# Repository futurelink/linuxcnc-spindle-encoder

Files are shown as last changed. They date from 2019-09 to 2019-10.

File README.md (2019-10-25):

# Incremental encoder Modbus RTU interface

This device is an interface to read incremental encoder meanings with Modbus.
It supports encoders from 100 to 1000PPR and interpolate position up to 4 times, 
so maximum resolutuion is 4000PPR. 

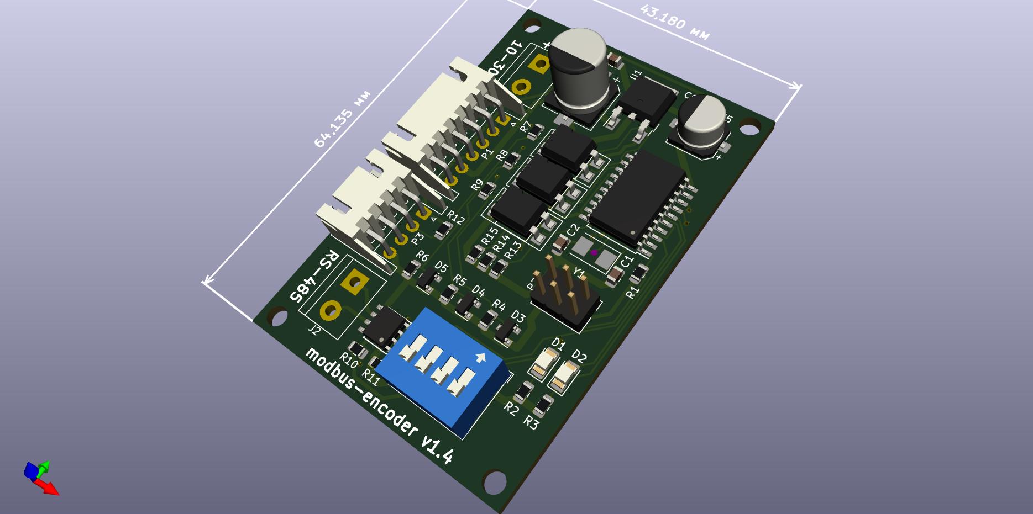
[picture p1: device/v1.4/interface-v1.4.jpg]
Device KiCAD 3D view


It's tested on 1000PPR encoder and it reads correct values on about 1000RPMs on internal 8MHz
ATtiny2313 RC oscillator, and about 2000PPM on 16MHz crystal.

## What does it do?

This small attiny2313 module and LinuxCNC component allows you to connect almost any precision encoder into LinuxCNC
and it works even if it has no Z phase output.

It allows your lathe execute G33, G33.1 (synchronized motion) and G76 (threading) canned cycles and 
use G96 (constant surface speed) spindle control strategy.

## Modbus

Device has slave ID 0x85. There are 6 16bit analog registers starting from reference address 0x00,
containing (0)heartbeat, (1)current position, (2)position increment, (3)current speed in RPM, (4)current Z-index value
and (5)encoder direction.

Device UART speed is 38400bps.

## Connection to LinuxCNC

Go to ./linuxcnc and execute:

```
$ sudo make
```

This will install component into your LinuxCNC.

Then you need this component in your HAL:

```
loadrt spindle_encoder
addf spindle-encoder.0 servo-thread
setp spindle-encoder.0.ppr 4096
net spindle-heartbeat  spindle-encoder.0.heartbeat <= mb2hal.spindle-encoder.heartbeat.int
net spindle-pos-in     spindle-encoder.0.pos-in <= mb2hal.spindle-encoder.pos-in.float
net spindle-pos-out    spindle-encoder.0.pos-out => motion.spindle-revs
net spindle-speed-rpm  spindle-encoder.0.speed-rpm <= mb2hal.spindle-encoder.speed-rpm.int
net spindle-speed      spindle-encoder.0.speed-rps => motion.spindle-speed-in
net spindle-index      spindle-encoder.0.index-in <= mb2hal.spindle-encoder.index.int
net spindle-index-ena  spindle-encoder.0.index-enable <=> motion.spindle-index-enable
net spindle-dir        spindle-encoder.0.direction <= mb2hal.spindle-encoder.direction.int
```

Also you'll need to load mb2hal module into userspace:

```
loadusr -W mb2hal config=modbus_config.ini
```

Copy modbus_config.ini from ./linuxcnc into your lathe configuration directory. Write your serial 
port device to SERIAL_PORT option in that ini file. Correct SERIAL_DELAY_MS if you need.

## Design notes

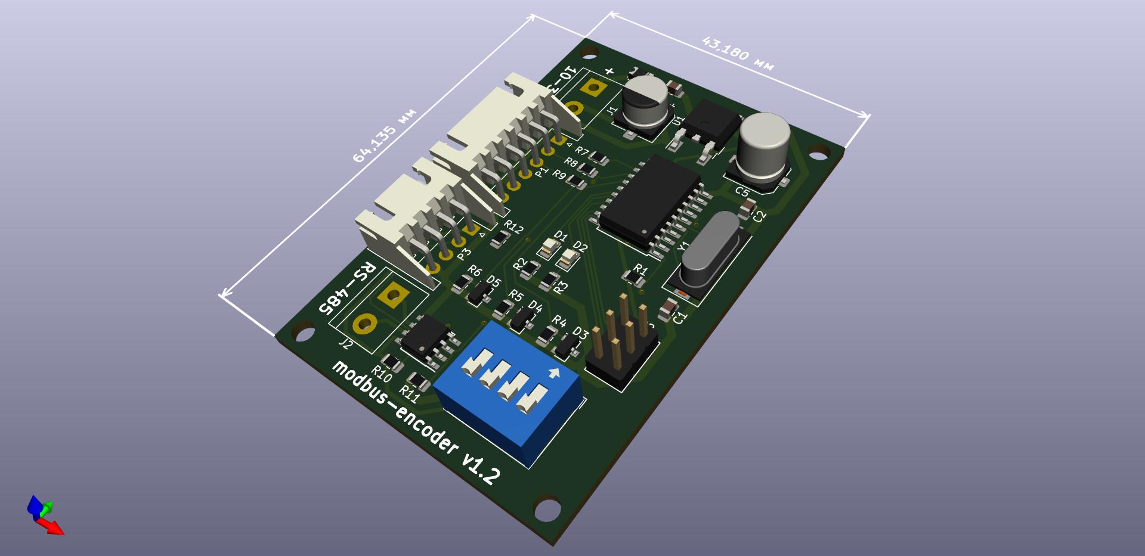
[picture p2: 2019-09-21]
device/interface-v1.2.jpg

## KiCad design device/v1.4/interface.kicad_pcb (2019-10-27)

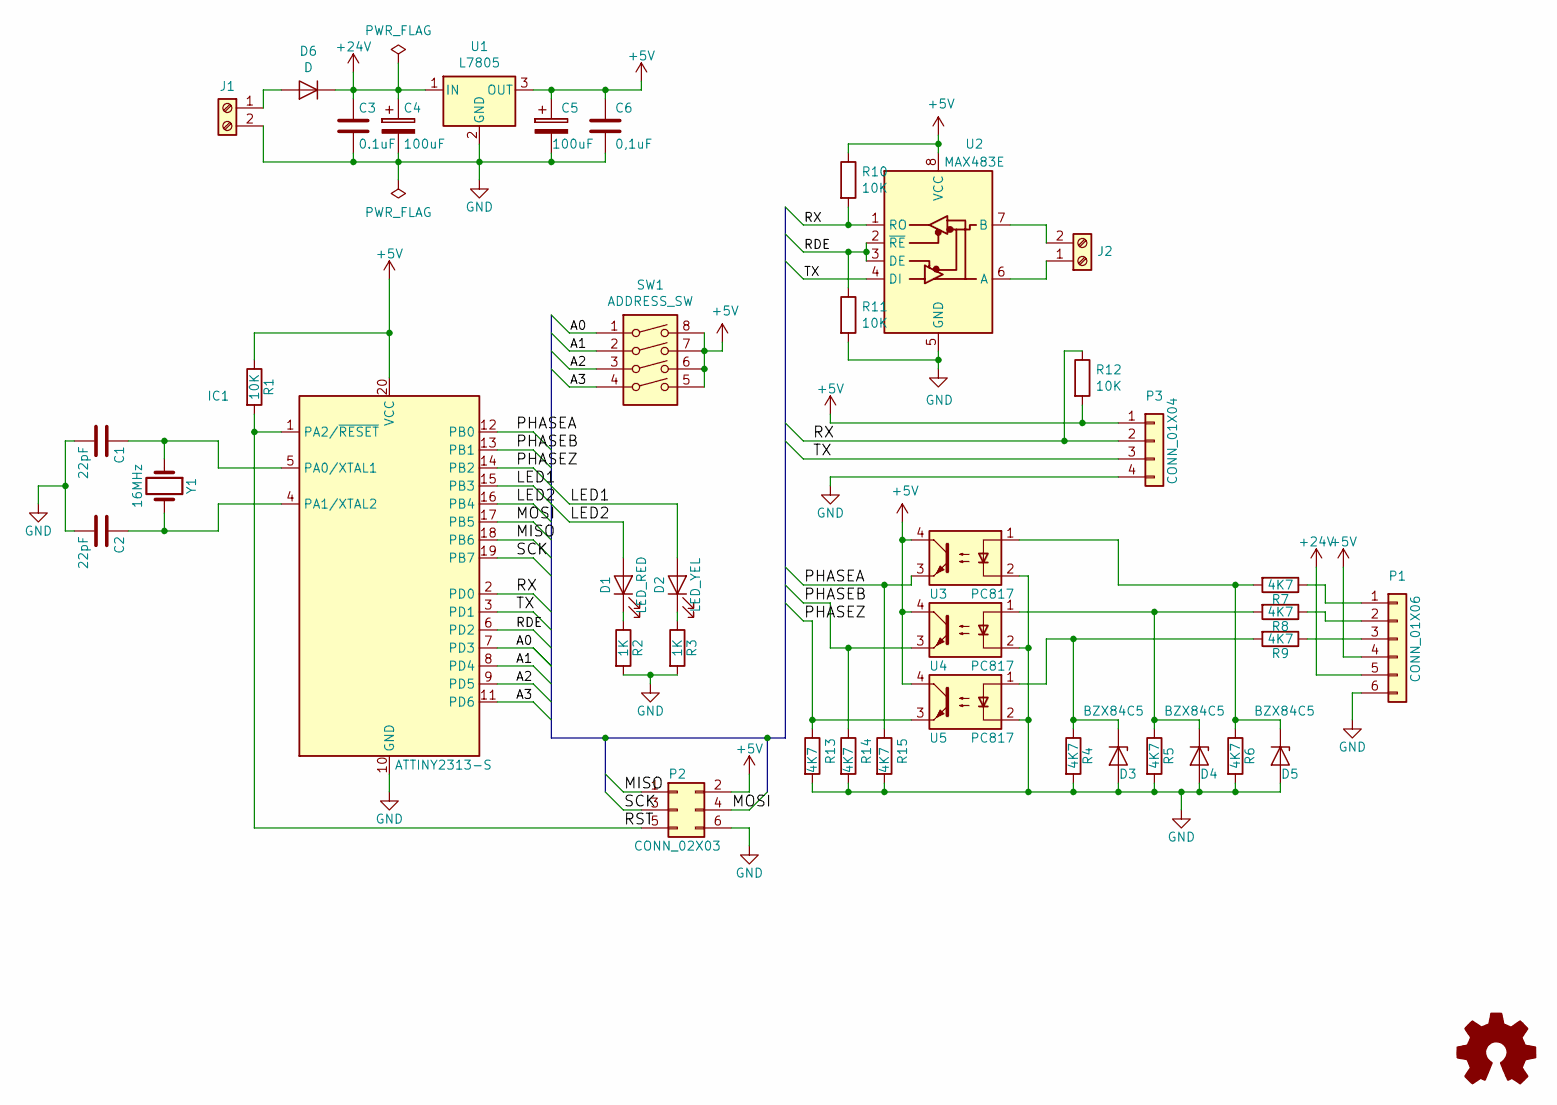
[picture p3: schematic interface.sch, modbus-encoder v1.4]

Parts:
C1, C2: 22pF; C_0805_2012Metric
C3: 0.1uF; C_0805_2012Metric
C4: 100uF; CP_Elec_8x10.5
C5: 100uF; CP_Elec_6.3x5.3
C6: 0,1uF; C_0805_2012Metric
D1: LED_RED; LED_1206_3216Metric
D2: LED_YEL; LED_1206_3216Metric
D3, D4, D5: BZX84C5; D_SOT-23_ANK
D6: D; D_1206_3216Metric
IC1: ATTINY2313-S; SOIC-20W_7.5x12.8mm_P1.27mm
J1: Screw_Terminal_1x02; TerminalBlock_bornier-2_P5.08mm
J2: Screw_Terminal_01x02; TerminalBlock_bornier-2_P5.08mm
P1: CONN_01X06; JST_XH_S6B-XH-A_1x06_P2.50mm_Horizontal
P2: CONN_02X03; PinHeader_2x03_P2.54mm_Vertical
P3: CONN_01X04; JST_XH_S4B-XH-A_1x04_P2.50mm_Horizontal
R1, R10, R11, R12: 10K; R_0805_2012Metric
R2, R3: 1K; R_0805_2012Metric
R4, R5, R6, R7, R8, R9, R13, R14, R15: 4K7; R_0805_2012Metric
SW1: ADDRESS_SW; SW_DIP_SPSTx04_Slide_9.78x12.34mm_W7.62mm_P2.54mm
U1: L7805; TO-252-2
U2: MAX483E; SOIC-8_3.9x4.9mm_P1.27mm
U3, U4, U5: PC817; DIP-4_W7.62mm_SMDSocket_SmallPads
Y1: 16MHz; Crystal_SMD_5032-2Pin_5.0x3.2mm

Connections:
+5V: C5.1, C6.1, IC1.20 (VCC), P1.4, P2.2, P3.1, R1.1, R10.1, R12.2, SW1.5, SW1.6, SW1.7, SW1.8, U1.3 (OUT), U2.8 (VCC), U3.4, U4.4, U5.4
+24V: C3.1, C4.1, D6.1 (K), P1.5, U1.1 (IN)
/A0: IC1.7 (PD3), SW1.1
/A1: IC1.8 (PD4), SW1.2
/A2: IC1.9 (PD5), SW1.3
/A3: IC1.11 (PD6), SW1.4
/LED1: D2.2 (A), IC1.15 (PB3)
/LED2: D1.2 (A), IC1.16 (PB4)
/MISO: IC1.18 (PB6), P2.1
/MOSI: IC1.17 (PB5), P2.4
/PHASEA: IC1.12 (PB0), R15.1, U3.3
/PHASEB: IC1.13 (PB1), R14.1, U4.3
/PHASEZ: IC1.14 (PB2), R13.1, U5.3
/RDE: IC1.6 (PD2), R11.1, U2.2 (~RE), U2.3 (DE)
/RST: IC1.1 (PA2/~RESET), P2.5, R1.2
/RX: IC1.2 (PD0), P3.2, R10.2, R12.1, U2.1 (RO)
/SCK: IC1.19 (PB7), P2.3
/TX: IC1.3 (PD1), P3.3, U2.4 (DI)
GND: C1.2, C2.2, C3.2, C4.2, C5.2, C6.2, D3.2 (A), D4.2 (A), D5.2 (A), IC1.10 (GND), J1.2, P1.6, P2.6, P3.4, R2.2, R3.2, R4.2, R5.2, R6.2, R11.2, R13.2, R14.2, R15.2, U1.2 (GND), U2.5 (GND), U3.2, U4.2, U5.2
unnamed: C1.1, IC1.5 (PA0/XTAL1), Y1.1
unnamed: C2.1, IC1.4 (PA1/XTAL2), Y1.2
unnamed: D1.1 (K), R2.1
unnamed: D2.1 (K), R3.1
unnamed: D3.1 (K), R4.1, R9.2, U5.1
unnamed: D4.1 (K), R5.1, R8.2, U4.1
unnamed: D5.1 (K), R6.1, R7.2, U3.1
unnamed: D6.2 (A), J1.1
unnamed: J2.1, U2.6 (A)
unnamed: J2.2, U2.7 (B)
unnamed: P1.1, R7.1
unnamed: P1.2, R8.1
unnamed: P1.3, R9.1

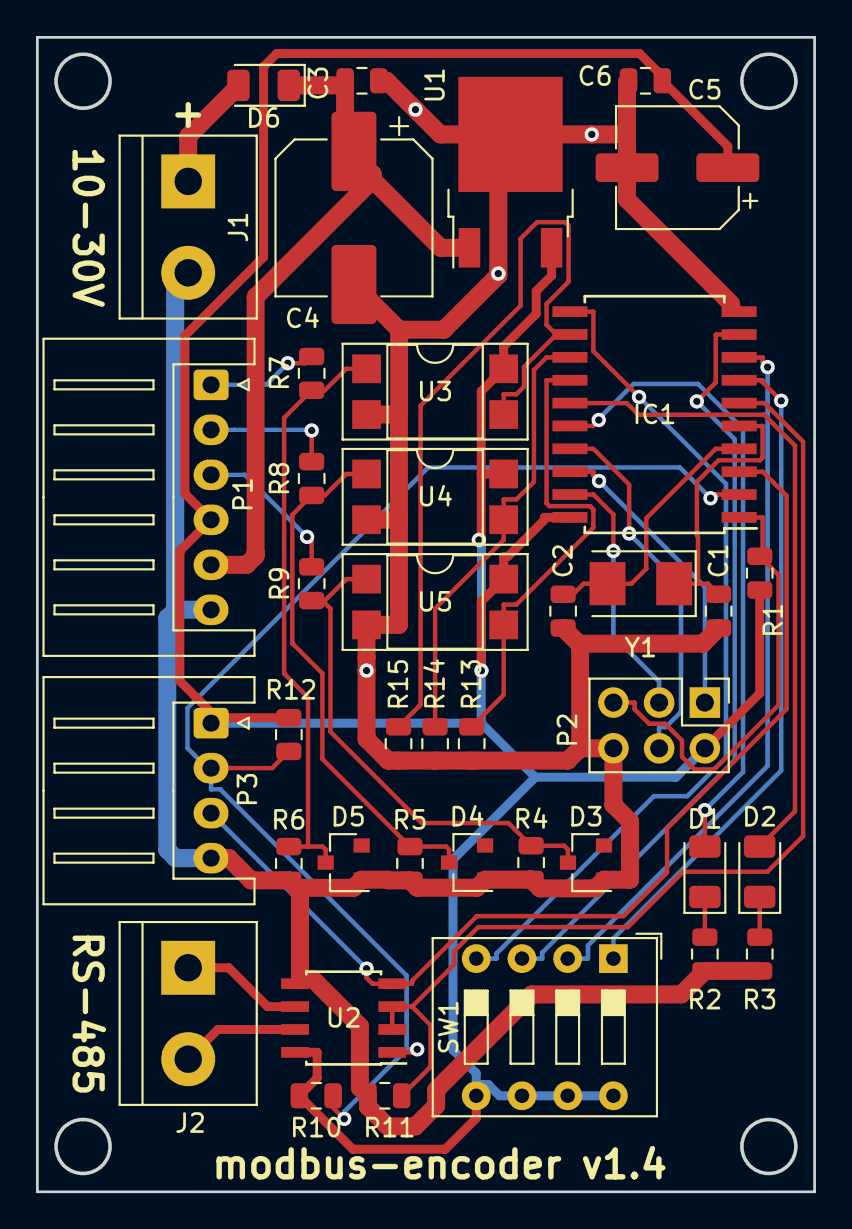
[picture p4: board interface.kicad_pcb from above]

Board: 2 copper layers, 43.2 x 64.1 mm, 40 parts (0 on the bottom side), 32 nets.

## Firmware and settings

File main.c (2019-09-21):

/*

Copyright 2019 Pavlov Denis <futurelink.vl@gmail.com>

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
*/

#include <avr/wdt.h>
#include <avr/io.h>
#include <avr/interrupt.h>

#include "config.h"

#define PARITY_NONE	0
#define PARITY_ODD	1
#define PARITY_EVEN	2

static void initPorts(void);
static void initUSART(uint8_t parity);
static void initTimer1(uint8_t timeout50usTicks);
static void initTimer0(void);

extern uint8_t slaveAddr;
extern volatile uint8_t sentLength;
extern volatile uint8_t sendLength;
extern uint8_t sendBuffer[];

int main(void) {
    asm("WDR");
    MCUSR &= ~(1 << WDRF);
    WDTCSR |= (1 << WDCE) | (1 << WDE);
    WDTCSR = (1 << WDE) | (1 << WDP2) | (1 << WDP1); // Вотчдог через 1 сек

    initUSART(PARITY_NONE);
    initTimer1(35);
    initTimer0();
    initPorts();

    sei();

    PORTB |= (1 << RED_LED); // Индикатор включения
    while (1) asm volatile("nop" ::);

    return 0;
}

void initPorts() {
    GIMSK |= (1 << PCIE);					// Разрешаем прерывания PCINT
    PCMSK |= (1 << PCINT2) | (1 << PCINT1) | (1 << PCINT0);	// Срабатывает на PCINT0, PCINT1 и PCINT2
    DDRB = (1 << RED_LED) | (1 << YELLOW_LED);			// Выходы на индикацию
    DDRD |= (1 << PD2);		// MAX483 чтение-запись
    PORTD &= ~(1 << PD2);	// MAX483 на чтение
    PORTD |= (1 << PD6) | (1 << PD5) | (1 << PD4) | (1 << PD3);

    // Считаем смещение адреса слейва
    slaveAddr = SLAVE_ID + ((PIND & (1 << PD6) & (1 << PD5) & (1 << PD4) & (1 << PD3)) >> PD3);
}

void initUSART(uint8_t parity) {
    UBRRH = UBRRH_VALUE;
    UBRRL = UBRRL_VALUE;
    UCSRB |= ((1 << TXEN) | (1 << RXEN) | (1 << RXCIE));	// Включаем прием, передачу и прерывание по приему
    UCSRC |= ((1 << UCSZ0) | (1 << UCSZ1));			// 8 бит данных (может будет убрать, т.к. по-умолчанию)

    // Настройка четности
    switch (parity) {
        case PARITY_EVEN: UCSRC |= (1 << UPM1); break;
        case PARITY_ODD: UCSRC |= (1 << UPM1) | (1 << UPM0); break;
        case PARITY_NONE: break;
    }
}

// Инициализация таймера тишины, таймер должен срабатывать после определенного
// интервала, но после приема каждого байта зануляться. По нему определяется
// конец посылки от мастера. Сразу не запускаем, он запускается по приему байта.
// -----------------------------------------------------------------------------
// Таймаут задается параметром в 50-миллисекундных интервалах.
void initTimer1(uint8_t timeout50usTicks) {
    OCR1A = (TIMER1_FREQ * timeout50usTicks) / (TIMER1_50US_TICKS);
    TCCR1A = 0;
    TCCR1B = (1 << CS12) | (1 << CS10); // Делитель 1024
    TCCR1C = 0;
    TCNT1 = 0;				// Сбрасываем счетчик
    TIMSK |= (1 << OCIE1A);		// Разрешаем прерывание TIMER1_COMPA_vect
}

// Инициализация таймера счета скорости, таймер на 20мс (0.02с). Считает кол-во меток,
// проходящих за период, чтобы определить скорость вращения энкодера.
void initTimer0() {
    // Таймер восьмибитный, поэтому OCR0A не более 255 должен быть
    OCR0A =  (TIMER0_FREQ * TIMER0_PERIOD_MS) / 1000; // При 16мс это работает нормально.
    TCCR0A = 0;
    TCCR0B = (1 << CS02) | (1 << CS00); // Делитель 1024 при 8МГц T = 128мкс, при 16МГц T = 64мкс
    TCNT0 = 0;				// Сбрасываем счетчик
    TIMSK |= (1 << OCIE0A);		// Разрешаем прерывание TIMER1_COMPA_vect
}

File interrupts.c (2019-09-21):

/*

Copyright 2019 Pavlov Denis <futurelink.vl@gmail.com>

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
*/

#include <avr/interrupt.h>

#include "config.h"
#include "modbus.h"

extern int16_t encoderPPR;
extern int16_t registers[];

extern uint8_t recvLength;
extern uint8_t recvBuffer[];

extern uint8_t sentLength, sendLength;
extern uint8_t sendBuffer[];

// Локальные для данного файла
int16_t encDirectionMeasure;
uint8_t  encPhases, encPhasesPrev;
uint16_t encSpeedMeasure;

// Таблица приращений
static const int8_t incTable[16] = {0,-1,1,0,1,0,0,-1,-1,0,0,1,0,1,-1,0};

/* ---------------------------------------------------------------------*/

//
// Тут происходит отправка данных посылки
//
ISR(USART_UDRE_vect) {
    if (sentLength > sendLength) {
	PORTD &= ~(1 << PD2);			// MAX483 на чтение
	UCSRB &= ~((1 << UDRE) | (1 << TXEN));	// Запрещаем передачу
	PORTB &= ~(1 << YELLOW_LED);		// Погасим светодиод, передали сообщение
	sendLength = sentLength = 0;
    } else {
	PORTD |= (1 << PD2);			// MAX483 на запись
	PORTB |= (1 << YELLOW_LED);		// Зажжем светодиод, передаем сообщение
	UDR = sendBuffer[sentLength++];
    }
}

//
// Тут происходит заполнение данными нашей посылки
//
ISR(USART_RX_vect) {
    if (UCSRA & (1 << RXC)) {
	PORTB |= (1 << RED_LED);	// Зажжем светодиод метки индекса
	if (recvLength < RECV_BUFFER_MAX) {
	    recvBuffer[recvLength++] = UDR;
	}

	PORTB &= ~(1 << RED_LED);	// Погасим светодиод метки индекса

	// Включаем таймер тишины
	TCNT1 = 0;
	TCCR1B = (1 << CS12) | (1 << CS10);
    }
}

// В прерывании таймера если он таки сработал, значит прием данных завершен.
// Нужно очистить обрбаотать принятые данные, очистить буфер и сбросить таймер.
ISR(TIMER1_COMPA_vect) {
    // Выключаем таймер тишины, он сработал
    TCCR1B &= ~((1 << CS12) | (1 << CS10));

    // Если что-то принято, надо обработать
    if (recvLength > 0) {
	if (registers[REGISTER_INDEX]) PORTB |= (1 << RED_LED);	// Зажжем светодиод метки индекса
	if (parseDatagram()) {		// Обработаем посылку
	    recvLength = 0;		// Сбрасыаем приемный буфер
	    registers[REGISTER_POSITION_INC] = 0;		// Сбрасываем инкремент
	    registers[REGISTER_INDEX] = 0;			// Сбрасываем метку индекса
	    PORTB &= ~(1 << RED_LED);	// Погасим светодиод метки индекса
	}
    }
}

//
// Таймер счетчика скорости оборотов
//
ISR(TIMER0_COMPA_vect) {
    asm("WDR"); // Сбрабываем вотчдог

    // Определяем направление вращения. Определение направления
    // возможно толькое если у нас не сбросилась позиция, то есть
    // мы не прошил полный оборот. То есть пока выставлена метка
    // мы просто пропускаем этот замер.
    if (!registers[REGISTER_INDEX]) {
	// 0 - вращение в положительную сторону, 1 - в отрицательную
	registers[REGISTER_DIRECTION] = (encDirectionMeasure > registers[REGISTER_POSITION]); 
    }
    encDirectionMeasure = registers[REGISTER_POSITION];

    // Cчитаем обороты в минутуENCODER_Q нужен, чтобы знать насколько сократить
    // числа, чтобы все влазило в 16 бит
    registers[REGISTER_SPEED] = (encSpeedMeasure * 60 / TIMER0_PERIOD_MS * (1000 / ENCODER_Q)) /  (ENCODER_PPR / ENCODER_Q / 4);
    encSpeedMeasure = 0;
}

//
// Обработка сигналов энкодера
//
ISR(PCINT_vect) {
    // Считаем позицию по фазовому сдвигу
    uint8_t encPhases = PINB & 0x03; // PCINT0 + PCINT1
    int8_t inc = incTable[encPhasesPrev * 4 + encPhases];
    registers[REGISTER_POSITION] += inc;  // Позиция энкодера в метках
    registers[REGISTER_POSITION_INC] += inc; // Количество пройденных меток с момента последней передачи данных
    encPhasesPrev = encPhases;

    // Замер позиции для счетчика скорости по фазе А
    // Считаем только когда фаза А меняется с 0 на 1
    if ((PINB & 0x07) == 0x01)  {
	++encSpeedMeasure;
    }

#ifdef ENCODER_HAS_Z
    if (PINB & 0x04) {
	registers[REGISTER_POSITION] = 0;	// Метка Z сбрасывает позицию на 0
	registers[REGISTER_INDEX] = 1;		// Сохраняем данные что прошли метку Z
    }
#else
    // Метка Z эмулируется при переходе
    // через полный оборот или при переходе черео 0.
    int16_t pos = registers[REGISTER_POSITION];
    if ((pos >= ENCODER_PPR) || (pos <= -ENCODER_PPR) || (pos == 0)) {
	registers[REGISTER_POSITION] = 0;
	registers[REGISTER_INDEX] = 1;
    }
#endif
}

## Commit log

2019-09-08 added schematic pdf
2019-09-09 pin names in mb2hal
    [modbus_config.ini]
2019-09-13 device schematics and PCB
    [interface-B.Cu.gbr, interface-B.Mask.gbr, interface-Edge.Cuts.gbr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]
2019-09-13 remove ignored files
    [interface-B.Cu.gbr, interface-B.Mask.gbr, interface-Edge.Cuts.gbr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]
2019-09-13 pcb update
    [interface.kicad_pcb]
2019-09-13 added address switch
    [interface.dsn, interface.kicad_pcb, interface.sch]
2019-09-15 some changes
    [interface.kicad_pcb]
2019-09-17 uart pull uo
    [interface.kicad_pcb, interface.sch]
2019-09-21 pcb fix
    [interface.kicad_pcb]
2019-10-16 fixed Zener BZX84
    [interface.dsn, interface.kicad_pcb, interface.sch]
2019-10-25 added optocouplers
    [interface.dsn, interface.kicad_pcb, interface.sch]
2019-10-27 fill zone
    [interface.kicad_pcb]

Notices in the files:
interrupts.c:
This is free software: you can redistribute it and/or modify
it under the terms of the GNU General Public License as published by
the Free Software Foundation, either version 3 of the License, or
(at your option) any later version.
